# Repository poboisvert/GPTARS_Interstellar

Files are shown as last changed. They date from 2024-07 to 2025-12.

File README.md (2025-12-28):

# TARS from Interstellar x ChatGPT

- Telegram: [https://t.me/GPTARS](https://t.me/GPTARS)

- Original article: https://www.hackster.io/charlesdiaz/how-to-build-your-own-replica-of-tars-from-interstellar-224833#comments

- Vercel App: https://docs-tars-ai.vercel.app/build/3d_print

2025+ Updates: https://github.com/TARS-AI-Community/TARS-AI

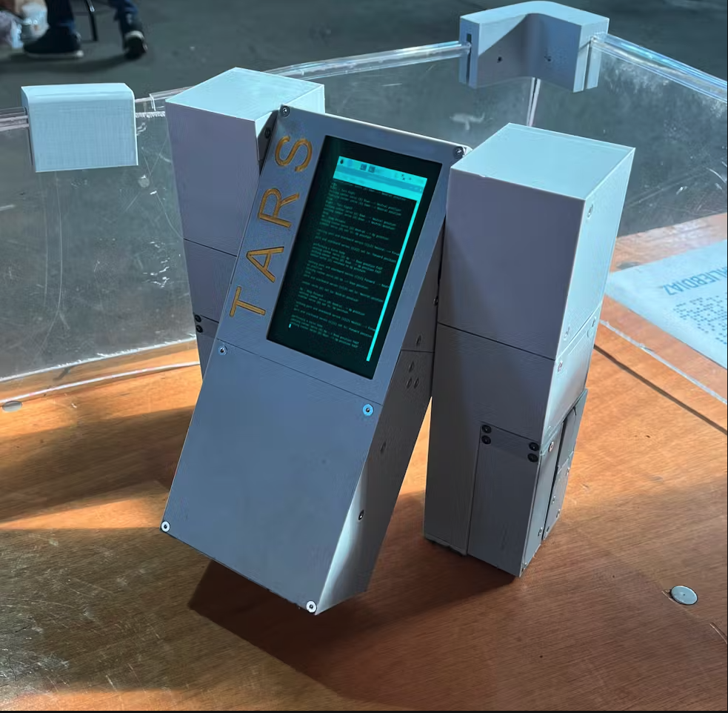
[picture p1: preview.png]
preview


## Files TARS v3_9 - Fix Case Clip

- DOWNLOAD: tars_3_v9_original.zip in repository

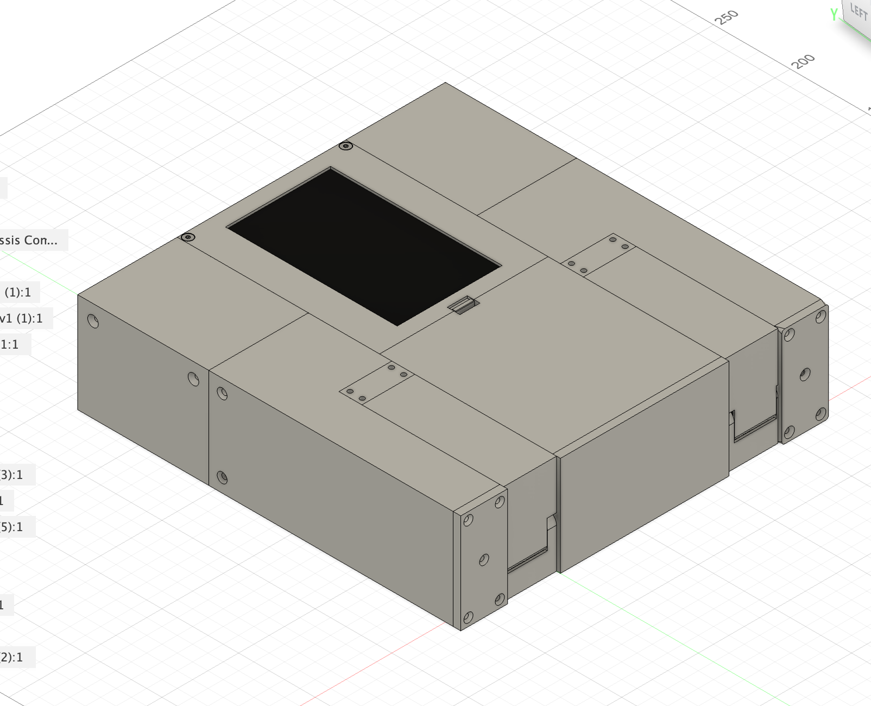
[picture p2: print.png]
print


## Software

- Fusion 360 at https://www.autodesk.com/ca-en/products/fusion-360/personal
- https://projects.raspberrypi.org/en/projects/getting-started-with-the-pico/2
- OS Pi: https://www.raspberrypi.com/software/

## Tutorial

- OS SD Card: https://www.tomshardware.com/how-to/set-up-raspberry-pi

### Adafruit 16-Channel PWM HAT with a Raspberry Pi

- Videos https://www.youtube.com/watch?v=bB-xymRI8BY,
- Documentation: https://learn.adafruit.com/adafruit-16-channel-pwm-servo-hat-for-raspberry-pi, https://core-electronics.com.au/guides/raspberry-pi/servo-hat-raspberry-pi/

### Without HAT

- Videos: https://www.youtube.com/watch?v=ea6tSppgZlY, https://www.youtube.com/watch?v=9jcEwn7GzNs, https://www.youtube.com/watch?v=40tZQPd3z8g
- Documentation: https://learn.adafruit.com/adafruits-raspberry-pi-lesson-8-using-a-servo-motor/overview, https://learn.adafruit.com/adafruit-16-channel-servo-driver-with-raspberry-pi/configuring-your-pi-for-i2c, https://www.youtube.com/watch?v=-x2EEIUMm6A

## 3D Printing

- Steel / Stainless / Aluminium: https://forgelabs.ca/
- PLA / ABS: https://jlc3dp.com/3d-printing-quote or https://www.treatstock.com/

## Hardware

#### Power

- 1 x 12V to 6V 3A DC at https://www.aliexpress.com/item/32968137531.html
- https://www.aliexpress.com/item/1005003160082010.html
- 1 x 5V DC 4A Fixed 2.1mm Tip Appliance Plugpack at https://www.amazon.ca/Power-Adapter-100-240V-Transformers-Supply/dp/B087LY41PV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
- 1 x 5V 4A DC Power Adapter at https://www.aliexpress.com/item/1005004589869667.html (Used for testing before buying battery)
- 1 x 5V USB To DC DC Power Cable 5.5\*2.1m at https://www.aliexpress.com/item/1005007296667037.html
- 200000mAh Portable Solar Power Bank External Battery Fast Charging Waterproof Powerbank with SOS Flashlight Poverbank for Xiaomi at https://www.aliexpress.com/item/1005006959367711.html, https://www.aliexpress.com/item/1005007306992861.html

Please use HDMI cable: fpv cable hdmi, HDMI-compatible,FPV HDMI ffc HDMI Ribbon Cable 90 Degree Mini/Micro HDMI to Standard HDMI PCB Connector 20pin fpv micro hdmi 15cm

---

#### Hardware

- See other guide: https://docs-tars-ai.vercel.app/build/bom to compare

- 1 x https://www.aliexpress.com/item/32914198349.html

- 2 x Lightweight Actobotics Servo Horn (H25T Spline) at https://www.servocity.com/25t-lightweight-hub-horn/ or look at .step file
- 1 x Adafruit 16-Channel 12-bit PWM/Servo Driver at https://www.adafruit.com/product/2327
- 1 x 8Bitdo Zero 2 Bluetooth at https://www.aliexpress.com/item/1005006458561670.html
-
- 5 x LD-3015MG 17KG 270 (LewanSoul LD-3015MG Standard Full Metal Gear Digital Servo with 17kg High Torque Dual Ball Bearing for RC Robot Car) at https://www.aliexpress.com/item/32787763122.html (2000-0025-0002)
- 1 x Fataba s3003 90-180deg at https://www.aliexpress.com/item/32957714272.html
- 4 x 2903-0004-0245 assembly at https://www.gobilda.com/2903-series-nylon-ball-linkage-m4-24-5mm-length-4-pack / Linkeage Rod M4 at https://www.aliexpress.com/item/1005005616106307.html
- 10 x Flexor bolts at https://www.aliexpress.com/item/32969042589.html

- 10 x Hex M3 20mm, 10 x Hex M3 10mm, 10 x Hex M3 14mm, 10 x Hex M3 30mm at https://www.aliexpress.com/item/1005003184392748.html
- 1 x Bearing 6x15x5 https://www.aliexpress.com/item/4000909583668.html
- 1 x Compression Spring 0.5mmx20mmx11mm https://www.aliexpress.com/item/1005005312536098.html, https://www.amazon.com/uxcell-Stainless-Compression-Spring-Capacity/dp/B09139BWH7

---

#### CPU & Storage

- 1 x MicroSD Card at https://www.aliexpress.com/item/1005006693506827.html
- 1 x Raspberri 3B/3B+ at https://www.adafruit.com/raspberrypi3bplus or eBay
- 1 x Elecrow 5 inch Touchscreen Portable Monitor HDMI-compatible 800x480 at https://www.aliexpress.com/item/32889893278.html

---

#### Battery

- 1 x myCharge Hub Mini at https://www.target.com/p/mycharge-hub-mini-3350mah-2-4a-output-power-bank-with-integrated-charging-cables-silver/-/A-76625534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
- 1 x Zeee 11.1V 120C 1500mAh 3S at https://www.amazon.ca/Zeee-Graphene-Quadcopter-Airplane-Helicopter/dp/B08P399N54/

## Extra

- Face Recognition: https://core-electronics.com.au/guides/face-identify-raspberry-pi/
- Lidar Detection: MS200 Lidar Sensor Kit Portable 360°TOF Ranging Scanner 12m Range Support ROS1 and ROS2 For ROS Robot Raspberry Pi Jetson NANO
- Battery Level: https://learn.sparkfun.com/tutorials/ltc4150-coulomb-counter-hookup-guide, https://forums.raspberrypi.com/viewtopic.php?t=173046, https://forums.raspberrypi.com/viewtopic.php?t=340930

## ChatGPT

- https://www.youtube.com/watch?v=N0718RfpuWE

## Servo Abstractor - Python

> Sort of redundant to give these functions their own file, but this program takes the basic servo movements from the servo controller file and combines them to automate walking functions.

## TARS Runner - Python

> Run this file in terminal on your onboard computer to initialize TARS. This file handles communication with the bluetooth remote.

## Servo Controller - Python

> Handles basic movements of servos in TARS. Communicates with an Adafruit PCA9685 servo driver to control the servos.

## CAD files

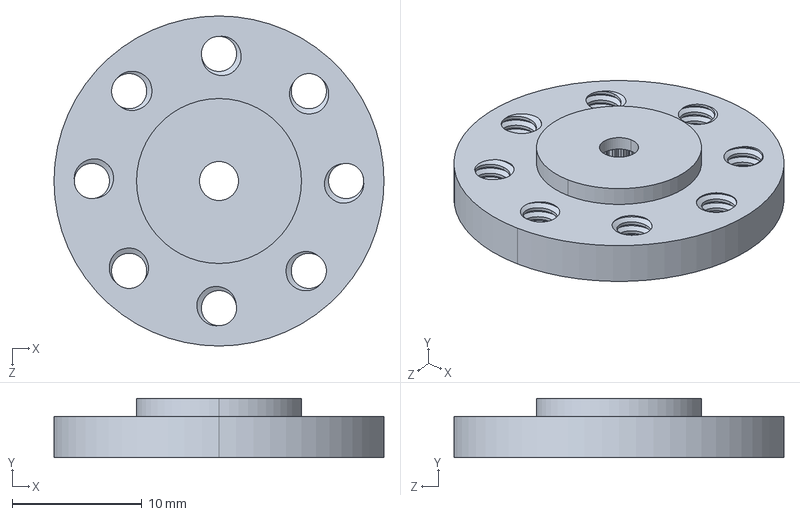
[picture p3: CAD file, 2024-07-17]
525125.STEP
25.4 x 4.57 x 25.4 mm

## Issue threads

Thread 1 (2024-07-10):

Printing the Parts

Tim-Gabrikowski, 2024-07-10:
Hello,

I am planning on building a GPTARS for myself and I was wondering, If all the parts could be printed using PLA, or if any parts need to be stronger and therefore need to be printed using steel/aluminium. I would probably say, if the whole casing is made of PLA, It would not be as heavy so it could handle it?

BTW: When I am really building it, I would like to contribute to this repo and provide more information I collect while building or programming...

poboisvert, 2024-07-10:
I am cleaning up the step files right now. The case shall be in PLA/ABS. Arms (the red in metal if possible) except to the case holder

Tim-Gabrikowski, 2024-07-10:
Could you export all the different parts as .stl files and name them in some way? So that Anyone can clearly see which part is which and needs to be printed with which material? Thanks!

Closed 2024-07-10.

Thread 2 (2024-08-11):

Feature: Add a camera and microphone so TARS can see you and hear you.

rkeshwani, 2024-08-11:
GPT models are now multi-modal so would be nice if the cad file had a spot for a camera that could be connected. Same goes for the microphone.

poboisvert, 2024-08-11:
You can find on Youtube tutorial to extrude the"spots" required to add microphone and camera

JFerguson576, 2024-08-12:
Hi guys,

Has anyone got working code for TARs CHATGPT integration (with voice and mobility control) that they are willing to share please?

Thank you.

John

John Ferguson
________________________________
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

rkeshwani, 2024-08-13:
You could use function calling from large language models to call python functions to connect to movement and other functionality. For voice I suggest taking a look at https://github.com/coqui-ai/TTS.

rkeshwani, 2024-08-13:
@poboisvert I'll take a look, not much recent experience with CAD. Do you have any free software suggestions? I have FreeCAD installed but I find the navigation a little clunky. Also, I was unable to download the file linked here but I was able to access the original. It seems at first glance that the hands are partially completed but might be due to my own ignorance around how the CAD software works. I see it is completed piecemeal. Example, no idea where smaller servos go. The arms appear to be partially completed but not linked to any servo. I am wanting to use aluminum for the outside and plastic for the inside but trying to figure out the best way to sort out the internal components.

SAMSAMPOP, 2024-08-13:
I too am struggling with the code for TARs CHATGPT integration.  Am currently working through the python scripts.  I have the internals assembled and just calling the tars_runner.py file.  I did get the servos working but it's stopped for some reason.  Anyway, if anyone has success with the TARS voice and is happy to share I would be super grateful.  Thank you

pyrater, 2024-11-24:
Has anyone been able to confirm the parts? the Step file shows https://www.amazon.com/gp/product/B083ZMZZCB/ref=ox_sc_act_title_1?smid=A333XEUDSX4WY3&psc=1 but the parts list here shows https://www.amazon.com/gp/product/B073F4TRSK/ref=ox_sc_act_title_12?smid=A1K1UK7O5KP6WQ&psc=1

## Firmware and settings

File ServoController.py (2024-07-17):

from __future__ import division
import time
import Adafruit_PCA9685
from threading import Thread

pwm = Adafruit_PCA9685.PCA9685()

# Set frequency to 60hz, good for servos.
pwm.set_pwm_freq(60)

portMain = 610
starMain = 200
portForarm = 570
starForarm = 200
portHand = 570
starHand = 240

# Center Lift Servo (0) Values
upHeight = 205
neutralHeight = 275
downHeight = 450

# Port Drive Servo (1) Values
forwardPort = 440
neutralPort = 375
backPort = 330

# Starboard Drive Servo (2) Values
forwardStarboard = 292
neutralStarboard = 357
backStarboard = 402

# moves the torso from a neutral position upwards, allowing the torso to pivot forwards or backwards
def height_neutral_to_up():
	height = neutralHeight
	print('setting center servo (0) Neutral --> Up position')
	while (height > upHeight):
		height = height - 1
		pwm.set_pwm(0, 0, height)
		time.sleep(0.001)
	print('center servo (0) set to: Up position\n ')

# rotates the torso outwards, enough so that when TARS pivots and lands, the bottom of the torso is 
# flush with the ground. Making the torso flush with the ground is an intentional improvement from
# previous programs, where TARS would land and then slide a little on smooth surfaces, which while
# allowing for a simple walking program, inhibited TARS' ability to walk on surfaces with different 
# coefficients of friction
def torso_neutral_to_forwards():
	port = neutralPort
	starboard = neutralStarboard
	print('setting port and starboard servos (1)(2) Neutral --> Forward')
	while (port < forwardPort):
		port = port + 1
		starboard = starboard - 1
		pwm.set_pwm(1, 1, port)
		pwm.set_pwm(2, 2, starboard)
		time.sleep(0.0001)
	print('port and starboard servos (1)(2) set to: Forward position\n ')

def torso_neutral_to_backwards():
	port = neutralPort
	starboard = neutralStarboard
	print('setting port and starboard servos (1)(2) Neutral --> Forward')
	while (port > backPort):
		port = port - 1
		starboard = starboard + 1
		pwm.set_pwm(1, 1, port)
		pwm.set_pwm(2, 2, starboard)
		time.sleep(0.0001)
	print('port and starboard servos (1)(2) set to: Forward position\n ')

# rapidly shifts the torso height from UP --> DOWN and then returns --> UP, which should cause TARS 
# to pivot and land on it's torso
def torso_bump():
	height = upHeight
	print('performing a torso bump\nsetting center servo (0) Up --> Down position FAST')
	while (height < downHeight):
		height = height + 2
		pwm.set_pwm(0, 0, height)
		time.sleep(0.000001)
	print('setting center servo (0) Down --> Up position FAST')
	while (height > upHeight):
		height = height - 1
		pwm.set_pwm(0, 0, height)
		time.sleep(0.0001)
	print('center servo (0) returned to Up position\n')
	
# returns the torso's vertical height and rotation to centered values from up height and forward 
# rotation. Activates two external functions so movement in both axes can occur in parallel.
def torso_return():
	t1 = Thread(target = torso_return_rotation)
	t2 = Thread(target = torso_return_vertical)
	
	t1.start()
	t2.start()

# returns torso's rotation to neutral from forward
def torso_return_rotation():
	port = forwardPort
	starboard = forwardStarboard
	print('setting port and starboard servos (1)(2) Forward --> Neutral position')
	while (port > neutralPort):
		port = port - 1
		starboard = starboard + 1
		pwm.set_pwm(1, 1, port)
		pwm.set_pwm(2, 2, starboard)
		time.sleep(0.005)
	print('port and starboard servos (1)(2) set to: Neutral position\n ')

# returns torso's vertical to neutral from up	
def torso_return_vertical():
	height = upHeight
	print('setting center servo (0) Up --> Down position')
	# moving the torso down to create clearance for the rotation of the legs
	while (height < downHeight):
		height = height + 1
		pwm.set_pwm(0, 0, height)
		time.sleep(0.00005)
	# moving the torso up from down to neutral
	#time.sleep(.2)
	while (height > neutralHeight):
		height = height - 1
		pwm.set_pwm(0, 0, height)
		time.sleep(0.00001)
	print('center servo (0) set to: Neutral position\n ')

def torso_return2():
	t1 = Thread(target = torso_return_rotation2)
	t2 = Thread(target = torso_return_vertical2)
	
	t1.start()
	t2.start()

# returns torso's rotation to neutral from forward
def torso_return_rotation2():
	port = backPort
	starboard = backStarboard
	print('setting port and starboard servos (1)(2) Forward --> Neutral position')
	while (port < neutralPort):
		port = port + 1
		starboard = starboard - 1
		pwm.set_pwm(1, 1, port)
		pwm.set_pwm(2, 2, starboard)
		time.sleep(0.01)
	print('port and starboard servos (1)(2) set to: Neutral position\n ')

# returns torso's vertical to neutral from up	
def torso_return_vertical2():
	height = upHeight
	print('setting center servo (0) Up --> Down position')
	# moving the torso down to create clearance for the rotation of the legs
	while (height < downHeight):
		height = height + 1
		pwm.set_pwm(0, 0, height)
		time.sleep(0.001)
	# moving the torso up from down to neutral
	time.sleep(.25)
	while (height > neutralHeight):
		height = height - 1
		pwm.set_pwm(0, 0, height)
		time.sleep(0.001)
	print('center servo (0) set to: Neutral position\n ')


# moves the torso from neutral position to down
def neutral_to_down():
    height = neutralHeight
    print('setting center servo (0) Neutral --> Down position')
    while (height < downHeight):
        height = height + 1
        pwm.set_pwm(0, 0, height)
        time.sleep(0.001)
        
def down_to_up():
    height = downHeight
    print('setting center servo (0) Down --> Neutral position')
    while (height > upHeight):
        height = height - 1
        pwm.set_pwm(0, 0, height)
        time.sleep(0.001)

def down_to_neutral():
    height = downHeight
    print('setting center servo (0) Down --> Neutral position')
    while (height > neutralHeight):
        height = height - 1
        pwm.set_pwm(0, 0, height)
        time.sleep(0.001)

def neutral_to_down():
    height = neutralHeight
    print('setting center servo (0) Down --> Neutral position')
    while (height < downHeight):
        height = height + 1
        pwm.set_pwm(0, 0, height)
        time.sleep(0.001)


def turn_right():
    port = neutralPort
    starboard = neutralStarboard
    while (port < forwardPort):
        port = port + 1
        starboard = starboard + 1
        pwm.set_pwm(1, 1, port)
        pwm.set_pwm(2, 2, starboard)
        time.sleep(0.001)
        
def turn_left():
    port = neutralPort
    starboard = neutralStarboard
    while (port > backPort):
        port = port - 1
        starboard = starboard - 1
        pwm.set_pwm(1, 1, port)
        pwm.set_pwm(2, 2, starboard)
        time.sleep(0.001)
        
def neutral_from_right():
    port = forwardPort
    starboard = backStarboard
    while (port > neutralPort):
        port = port - 1
        starboard = starboard - 1
        pwm.set_pwm(1, 1, port)
        pwm.set_pwm(2, 2, starboard)
        time.sleep(0.005)
    pwm.set_pwm(1, 1, neutralPort)
    pwm.set_pwm(2, 2, neutralStarboard)
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

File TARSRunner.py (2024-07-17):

import evdev
import time
import TARS_Servo_Abstractor3
import TARS_Servo_Controller3
from evdev import InputDevice, categorize, ecodes
import Adafruit_PCA9685

pwm = Adafruit_PCA9685.PCA9685()

#port
pwm.set_pwm(3, 3, 610)
pwm.set_pwm(4, 4, 570)
pwm.set_pwm(5, 5, 570)
#starboard
pwm.set_pwm(6, 6, 200)
pwm.set_pwm(7, 7, 200)
pwm.set_pwm(8, 8, 240)

# Set frequency to 60hz, good for servos.
pwm.set_pwm_freq(60)

gamepad = InputDevice('/dev/input/event3')

lTrg = 37
rTrg = 50
upBtn = 46
downBtn = 32
lBtn = 18
rBtn = 33
xBtn = 23
yBtn = 35
aBtn = 36
bBtn = 34
minusBtn = 49
plusBtn = 24

toggle = True
pose = False

print(gamepad)

for event in gamepad.read_loop():
    if event.type == ecodes.EV_KEY:
        if event.value == 1:
            if event.code == lTrg:
                print("Left Trigger")
                if toggle == True:
                    TARS_Servo_Controller3.portMainPlus()
                elif toggle == False:
                    TARS_Servo_Controller3.portMainMinus()
            elif event.code == rTrg:
                print("Right Trigger")
                if toggle == True:
                    TARS_Servo_Controller3.starMainPlus()
                elif toggle == False:
                    TARS_Servo_Controller3.starMainMinus()
            elif event.code == upBtn:
                print("Up - Step Forward")
                TARS_Servo_Abstractor3.stepForward()
            elif event.code == downBtn:
                print("Down")
                if pose == False:
                    TARS_Servo_Abstractor3.pose()
                    pose = True
                elif pose == True:
                    TARS_Servo_Abstractor3.unpose()
                    pose = False
            elif event.code == lBtn:
                print("Left - Turn Left")
                TARS_Servo_Abstractor3.turnLeft()
            elif event.code == rBtn:
                print("Right - Turn Right")
                TARS_Servo_Abstractor3.turnRight()
            elif event.code == xBtn:
                print("X")
                if toggle == True:
                    TARS_Servo_Controller3.starForarmPlus()
                elif toggle == False:
                    TARS_Servo_Controller3.starForarmMinus()
            elif event.code == yBtn:
                print("Y")
                if toggle == True:
                    TARS_Servo_Controller3.portForarmPlus()
                elif toggle == False:
                    TARS_Servo_Controller3.portForarmMinus()
            elif event.code == aBtn:
                print("A")
                if toggle == True:
                    TARS_Servo_Controller3.starHandPlus()
                elif toggle == False:
                    TARS_Servo_Controller3.starHandMinus()
            elif event.code == bBtn:
                print("B")
                if toggle == True:
                    TARS_Servo_Controller3.portHandPlus()
                elif toggle == False:
                    TARS_Servo_Controller3.portHandMinus()
            elif event.code == plusBtn:
                print("+")
                toggle = True
            elif event.code == minusBtn:
                print("-")
                toggle = False
        elif event.value == 0:
            print("Stop")
